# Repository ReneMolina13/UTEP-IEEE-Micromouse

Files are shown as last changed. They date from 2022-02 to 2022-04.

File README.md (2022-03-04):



<!-- PROJECT LOGO -->
</br>
<div align="center">
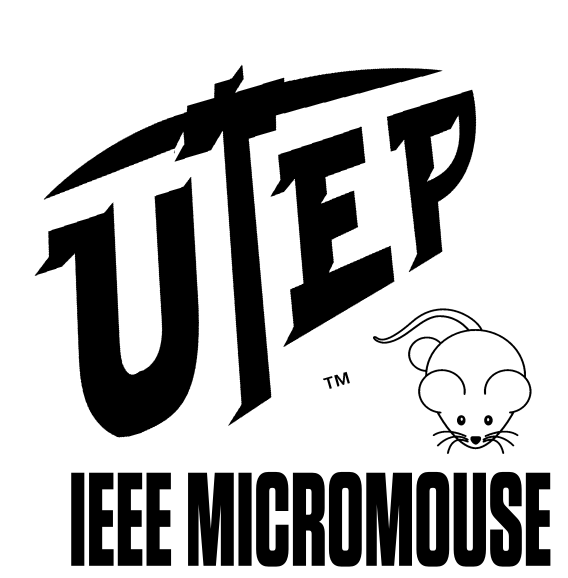
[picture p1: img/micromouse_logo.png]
  
  <h3 align="center">UTEP IEEE Micromouse</h3>
   <p align="center">
     UTEP IEEE Micromouse project repository
     </br>
     <a href="workshops/Intro to micromouse presentation.pdf"><strong>See intro presentation</strong></a>
     </br>
  </p>
</div>

<!-- TABLE OF CONTENTS -->
<details>
  <summary>Table of Contents</summary>
  <ol>
    <li><a href="#about-the-project">About The Project</a></li>
    <li><a href="#contributing">Contributing</a></li>
    <li><a href="#license">License</a></li>
    <li><a href="#contact">Contact</a></li>
    <li><a href="#acknowledgments">Acknowledgments</a></li>
  </ol>
</details>

<!-- ABOUT THE PROJECT -->
## About The Project
</br>
<div align="left">
  IEEE UTEP Micromouse repository where you can find template code, schematics and workshops
  to build and get your mouse working. This repository was designed to be used with the micromouse
  kit shown in the schematics folder. The workshops will guide you through the necessary code to 
  have your mouse solving a micromouse maze.
  
  Take a look at:
  
  - [Schematics](micromouse_arduino_nano_kit/Micromouse_Arduino_Nano.pdf)
  - [Workshops](workshops/)
  - [Code](code_template/)
</div>

<p align="right">(<a href="#top">back to top</a>)</p>

<!-- CONTRIBUTING -->
## Contributing

To contribute, please fork the project and send a pull request or talk to any of the UTEP IEEE officers. For any other questions please use the contact info at the bottom to contact the owner of this repository.
<p align="right">(<a href="#top">back to top</a>)</p>

<!-- LICENSE -->
## License

Distributed under the MIT License. See `LICENSE.txt` for more information.

<p align="right">(<a href="#top">back to top</a>)</p>

<!-- CONTACT -->
## Contact

Alejandro Martinez Acosta - amartinezacosta@miners.utep.edu

Project Link: [https://github.com/amartinezacosta/UTEP-IEEE-Micromouse](https://github.com/amartinezacosta/UTEP-IEEE-Micromouse)

<p align="right">(<a href="#top">back to top</a>)</p>

<!-- ACKNOWLEDGMENTS -->
## Acknowledgments
[University of Texas at El Paso](https://www.utep.edu/)

[IEEE University of Texas at El Paso branch](https://edu.ieee.org/us-utep/)

<p align="right">(<a href="#top">back to top</a>)</p>

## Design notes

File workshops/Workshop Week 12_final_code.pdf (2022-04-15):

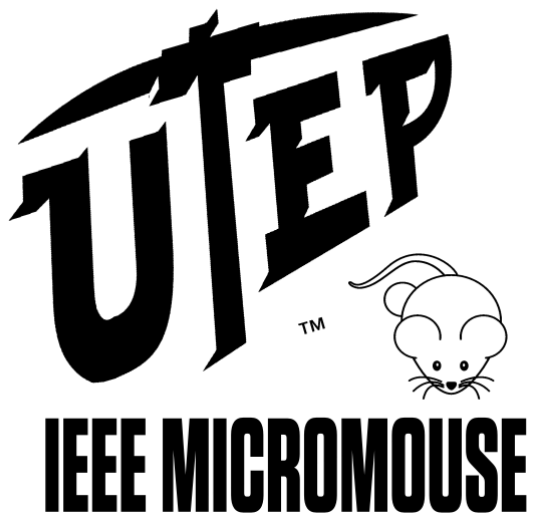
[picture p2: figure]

# Workshop Week 12: Scan walls, bestneighbor, and turn to neighbor

2

## Objective:

## Finish the micromouse code with the final algorithm to reach the center of the maze by

completing the missing code, such as scanning for walls, finding the best neighbor and turning towards the best neighbor.

## Background information:

This week we will look at the final portions of code to solve the maze, thus completing the micromouse project. Last workshop, you were able to find the best path possible to the center of the maze by using the flood fill algorithm. The exercise for the last workshop was to manually

## move the mouse around the maze. Today we will automate the process by writing a set of

functions that will find the best neighbor (open neighbor with lowest cell value), turn towards the best neighbor and scan the maze for new walls.

Before tackling those functions, let us start by thinking about the main and final algorithm to solve the maze. First, we want to run the program until we reach the 0 valued cell. Second, we

## want to always orient and move towards the neighbor that is open and has the lowest cell value. Finally, the mouse must update its position and orientation on the maze as well as

physically on the real maze. In addition, the mouse must add walls to the maze as they are encountered.

## With those requirements in mind, here is the final algorithm to solve the maze:

1. void loop()
2. {
3. /*Get the initial position and heading of the mouse*/
4. int8_t x = mouse_get_x();
5. int8_t y = mouse_get_y();
6. uint8_t heading = mouse_get_heading();
7.
8. /*Run the algorithm until we reached the zero value cell (Center of the maze)*/
9. do
10. {
11. /*Wait for button press or serial console for debugging (Not needed)*/
12. while(digitalRead(BUTTON) != HIGH);
13.
14. /*Scan walls*/
15. scan_walls(x, y, heading);
16.
17. /*Update maze using floodfill*/
18. flood_fill(x, y);
19.
20. /*Get the best neighbor*/
21. uint8_t best_neighbor = find_best_neighbor(x, y); 22.
23. /*Orient mouse towards best neighbor*/
24. turn_best_neighor(best_neighbor);
25.
26. /*Move forward*/
27. move_forward(x, y, best_neighbor);
28.
29. /*Get the position and heading of the mouse*/
30. x = mouse_get_x();

3

31. y = mouse_get_y();
32. heading = mouse_get_heading();
33.
34. /*Print maze, only for debugging (Not needed)*/
35. maze_print();
36. }while(maze_get_value(x, y) != 0);
37.
38. /*Maze solved trap the CPU*/
39. while(1);
40. }
41.

As you can observe, we are placing the final portion of code in the loop function. This is not required, because once we reached the center of the maze, we want to finish our program. You might want to play around and explore on what to do next after we find the center of the maze. One thing that you might consider is to do a second run with the maze already mapped out and with a valid path to center, but this time the mouse does it as fast as possible.

## Scan walls

## To scan the walls, the mouse simply must take a reading on all sensors and check if the

measurements are greater than the wall thresholds.

Now it is easy to think that if the right or left sensor measurements is greater than a threshold, then we simply add a wall to the EAST or WEST. This in fact will give you the wrong result because the orientation of the mouse is not always aligned to the NORTH of the maze and the

## walls are relative to it. Here is a visual example of why this happens:

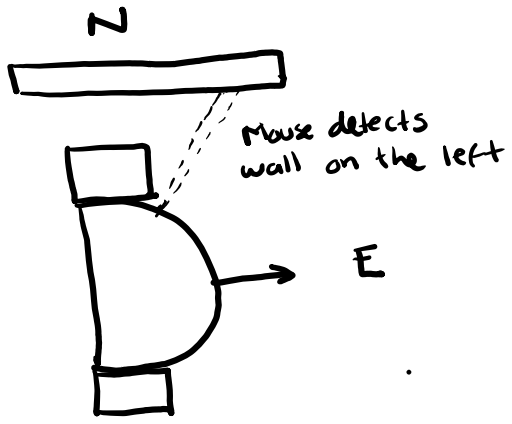
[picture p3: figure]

Figure 1 Adding walls to the maze depends on the orientation of the mouse. The mouse is heading EAST, but we detected a wall on our left. If we simply add the left sensor as an EAST wall, then we will get the wrong wall placement

4

Looking at the image above, you can see that the mouse detected a wall to the left of its sensor. You might be tempted to add the WEST wall of the current cell, but that will be wrong because of the orientation of the mouse. The correct answer is to add a wall to the NORTH. To solve this problem, we are going to shift the orientation of the wall discovered by 1 or 3 depending on the

## heading of the mouse. So, for the image above, we simply shift the current heading of the mouse heading by 3, so we move from EAST to SOUTH to WEST and the finally to NORTH, which

is the correct position of the discovered wall. if we discover a wall to our right, we take the same approach but this time we only shift the wall orientation by one. This is the code to add a

## wall when the left IR sensor measurement is greater than a threshold:

1. /*Threshold for left sensor*/
2. if(ir2 > IR_LEFT_WALL_THRESHOLD)
3. {
4. /*There is a wall on our right*/
5. /*Bit shift heading for correct wall positioning*/
6. uint8_t wall = heading << 3;
7. /*If bigger than 16, then wrap around back to 1*/
8. if(wall > 8)
9. {
10. wall /= 16;
11. }
12.
13. maze_set_wall(x, y, wall);
14. }
15.

Notice that we need to wrap around the wall if it ever gets bigger than 8, this is due to the internal implementation of the maze, and it should be added to your code.

## The final code to scan for walls will look like this:

1. const int IR_FRONT_WALL_THRESHOLD = 700;
2. const int IR_RIGHT_WALL_THRESHOLD = 700;
3. const int IR_LEFT_WALL_THRESHOLD = 700;
4.
5. void scan_walls(int x, int y, uint8_t heading)
6. {
7. /*Measure all IR sensors*/
8. int ir0 = ir_0_read(150);
9. int ir1 = ir_1_read(150);
10. int ir2 = ir_2_read(150);
11. int ir3 = ir_3_read(150);
12.
13. /*Threshold for front sensors*/
14. int ir_front = (ir0 + ir3)/2;
15. if(ir_front > IR_FRONT_WALL_THRESHOLD)
16. {
17. /*There is a wall at the front*/
18. /*Just set the wall to the current heading of the mouse*/
19. maze_set_wall(x, y, heading);
20. }
21.
22. /*Threshold for right sensor*/
23. if(ir1 > IR_RIGHT_WALL_THRESHOLD)
24. {
25. /*There is a wall on our left*/

5

26. /*Bit shift heading for correct wall positioning*/
27. uint8_t wall = heading << 1;
28. /*If bigger than 16, then wrap around back to 1*/
29. if(wall > 8)
30. {
31. wall /= 16;
32. }
33.
34. maze_set_wall(x, y, wall);
35. }
36.
37. /*Threshold for left sensor*/
38. if(ir2 > IR_LEFT_WALL_THRESHOLD)
39. {
40. /*There is a wall on our right*/
41. /*Bit shift heading for correct wall positioning*/
42. uint8_t wall = heading << 3;
43. /*If bigger than 16, then wrap around back to 1*/
44. if(wall > 8)
45. {
46. wall /= 16;
47. }
48.
49. maze_set_wall(x, y, wall);
50. }
51. }
52.

## Find best neighbor

Next up is finding the best neighbor. The best neighbor is always going to be the open cell with the lowest cell value. If you look at the flood fill algorithm, you can observe that there is a section that also tries to find the neighbor with the lowest minimum value. So, we can simply

## repeat that implementation as follows:

1. uint8_t find_best_neighbor(int x, int y)
2. {
3. /*Neighbor offsets for all orientations*/
4. int8_t neighbor_offset[4][2] =
5. {
6. {0, -1},
7. {1, 0},
8. {0, 1},
9. {-1, 0},
10. };
11.
12. /*Get current cell*/
13. cell_t *current = maze_get_cell(x, y);
14. cell_t *neighbor_cell;
15.
16. /*Assume lowest value is the highest distance*/
17. uint8_t lowest_value = 255;
18. /*Assume best neighbor is to the north*/
19. uint8_t best_neighbor = NORTH;
20. for(int i = 0; i < 4; i++)
21. {
22. /*If the neighbor is open...*/
23. if((current->walls & (1 << i)) == 0)

6

24. {
25. /*Get neighbor coordinates*/
26. int8_t nx = x + neighbor_offset[i][0];
27. int8_t ny = y + neighbor_offset[i][1]; 28.
29. /*Get neighbor cell value*/
30. neighbor_cell = maze_get_cell(nx, ny);
31. if(neighbor_cell->value < lowest_value)
32. {
33. /*If this this lower than the previous cell value, then set it as
34. * the new minimum
35. */
36. lowest_value = neighbor_cell->value;
37. best_neighbor = (1 << i);
38. }
39. }
40. }
41.
42. return best_neighbor;
43. }
44.

Observe that we always assume that the best neighbor is to the north. We do this so that if we

## have 2 neighbors of the same value, we always select the one that does not make the mouse

turn.

## Turn towards best neighbor

The next function we need to tackle is turning towards the best neighbor. The input of this function is the desired heading, and the output will obviously be the mouse physically turning

## and the maze updating the heading of the mouse. To do this we must consider the current

heading of the mouse and the desired heading, which will come in the form of NORTH, EAST,

## SOUTH and WEST. Once we know this, we can now physically turn the mouse +90.0, -90.0 or

180.0 degrees.

## To know the angle the mouse has to turn, we must create a truth table as follows:

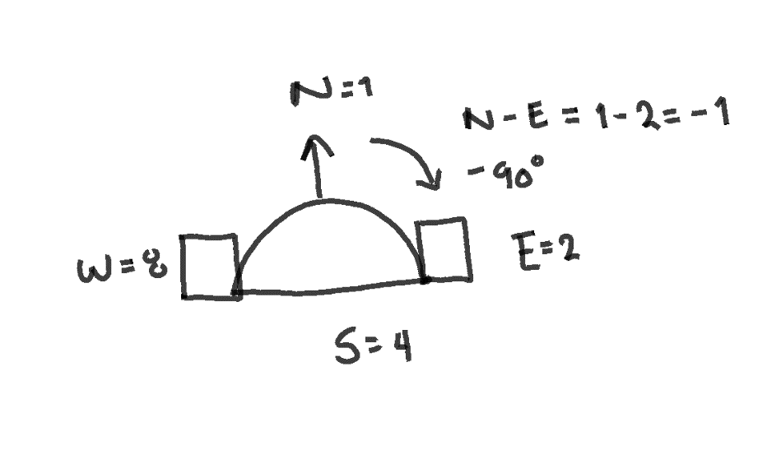
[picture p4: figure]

Figure 2 Basic idea on how we find how the angle and direction of rotation

7

Heading | New Heading | Heading - New Heading | Result
1 | 1 | 0 | 0°
1 | 2 | -1 | -90°
1 | 4 | -3 | 180°
1 | 8 | -7 | 90°
2 | 1 | 1 | 90°
2 | 2 | 0 | 0°
2 | 4 | -2 | -90°
2 | 8 | -6 | 180°
4 | 1 | 3 | 180°
4 | 2 | 2 | 90°
4 | 4 | 0 | 0°
4 | 8 | -4 | -90°
8 | 1 | 7 | -90°
8 | 2 | 6 | 180°
8 | 4 | 4 | 90°
8 | 8 | 0 | 0°
Figure 3 Truth table to turn the mouse based on current and desired heading

Using the table as our guide, we can create a switch statement (https://www.tutorialspoint.com/cprogramming/switch_statement_in_c.htm) to turn the mouse based on the

## result of the heading minus the new heading. The code looks as follows:

1. void turn_best_neighor(uint8_t best_neighbor)
2. {
3. /*Get current heading*/
4. uint8_t heading = mouse_get_heading();
5. /*Relative positioning to best neighbor*/
6. int8_t delta = heading - best_neighbor;
7.
8. /*Truth table to find how much we need to turn*/
9. switch(delta)
10. {
11. case 7: case -1: case -2: case -4:
12. /*Physically turn the mouse*/
13. control_turn(-90.0);
14. break;
15. case -7: case 1: case 2: case 4:
16. /*Physically turn the mouse*/
17. control_turn(90.0);
18. break;
19. case 3: case -3: case 6: case -6:
20. /*Physically turn the mouse*/
21. control_turn(180.0);
22. break;
23. }
24.
25. /*Update heading mouse*/
26. mouse_set_heading(best_neighbor);
27. }
28.

8

Notice that we are using the control_turn function from workshop 9. (https://github.com/amartinezacosta/UTEP-IEEE-Micromouse/blob/main/workshops/Workshop%20Week%209_Turn%20Control.pdf) If you don’t have this function, please go back to and complete this workshop.

## Move forward

## Lastly, we need to move the mouse forward AFTER we orient the mouse towards the best

neighbor. As with the turn_best_neighbor function, we first physically move the mouse, then

## update its position on the maze. The function to do this can be coded as follows:

1. void move_forward(int8_t x, int8_t y, uint8_t heading)
2. {
3. /*Physically move the mouse forward*/
4. control_forward();
5.
6. /*figure out where we need to move the mouse on the map*/
7. switch(heading)
8. {
9. case NORTH:
10. y--;
11. break;
12. case EAST:
13. x++;
14. break;
15. case SOUTH:
16. y++;
17. break;
18. case WEST:
19. x--;
20. break;
21. }
22.
23. /*Set the mouse new position on the map*/
24. mouse_set_x(x);
25. mouse_set_y(y);
26. }
27.

## Look at how we move the mouse based on the heading. Depending on the orientation of the

mouse, if we move forward one cell, then we either increment or decrement the x or y position of the mouse.

Finally, observe that we make use of the control_forward function, which was introduced in workshop 8. (https://github.com/amartinezacosta/UTEP-IEEE-Micromouse/blob/main/workshops/Workshop%20Week%208_Speed%20and%20Wall%20Control.pdf) Again, if you don’t have this function, please read the workshop and complete it.

9

## Exercise:

Complete the micromouse project by writing the scan_walls, find_best_neighbor,

## turn_best_neighbor and move_forward functions into your main sketch. Use the code

template below.

1. #include "micromouse.h"
2. #include "maze.h"
3.
4. uint8_t find_best_neighbor(int x, int y)
5. {
6. }
7.
8. void scan_walls(int x, int y, uint8_t heading)
9. {
10. }
11.
12. void turn_best_neighbor(uint8_t best_neighbor)
13. {
14. }
15.
16. void move_forward(int8_t x, int8_t y, uint8_t heading)
17. {
18. }
19.
20. void setup()
21. {
22. /*Enable serial port for bluetooth*/
23. Serial.begin(9600);
24.
25. /*Initialize maze*/
26. maze_init(MAZE_WIDTH/2, MAZE_HEIGHT/2);
27. mouse_set_x(0);
28. mouse_set_y(MAZE_HEIGHT - 1);
29. }
30.
31. void loop()
32. {
33. /*Get the initial position and heading of the mouse*/
34. int8_t x = mouse_get_x();
35. int8_t y = mouse_get_y();
36. uint8_t heading = mouse_get_heading();
37.
38. /*Run the algorithm until we reached the zero value cell (Center of the maze)*/
39. do
40. {
41. /*Wait for button press or serial console for debugging (Not needed)*/
42. while(digitalRead(BUTTON) != HIGH);
43.
44. /*Scan walls*/
45. //scan_walls(x, y, heading);
46.
47. /*Update maze using floodfill*/
48. flood_fill(x, y);
49.
50. /*Get the best neighbor*/
51. uint8_t best_neighbor = find_best_neighbor(x, y); 52.
53. /*Orient mouse towards best neighbor*/
54. turn_best_neighor(best_neighbor);
55.
56. /*Move forward*/

10

57. move_forward(x, y, best_neighbor);
58.
59. /*Get the position and heading of the mouse*/
60. x = mouse_get_x();
61. y = mouse_get_y();
62. heading = mouse_get_heading();
63.
64. /*Print maze, only for debugging (Not needed)*/
65. maze_print();
66. }while(maze_get_value(x, y) != 0);
67.
68. /*Maze solved trap the CPU*/
69. while(1);
70. }
71.

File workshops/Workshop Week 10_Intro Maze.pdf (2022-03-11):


# Workshop Week 10: Intro to Maze

2

Objective:

Learn how to represent a maze in C, and how to set the walls and values of the maze cells. Learn about data structures and how they can be used to represent a maze cell. Print the maze into a terminal to visualize the maze and mouse position.
Background information:

We are now moving into what we consider the second part of micromouse project, the maze/path planning software. In this second part, we will write the code to represent the maze inside the Arduino’s memory, scan for walls, find the best neighbor and orient the mouse towards the best neighbor. We will also start thinking about the end goal of the micromouse and working towards finishing the final algorithm of the micromouse project.

As of right now, our mouse can move a maze cell distance and turn accurately to a specified angle. This is great if we only want to move on a straight and turn mindlessly, but we know that the mouse should accomplish a specific task, which is reaching the center of the maze. To do this we need to have a path planning algorithm, and to do path planning we need a map of the mouse environment. The map of the micromouse is simple, 8x8 cells each with 4 walls on it’s NORTH, EAST, SOUTH and WEST borders. The cells on the borders can be assumed to always have a wall on its perimeter, so that leave us with mapping the rest of the cells on the maze.

In the interest of time, we will provide you with the code for the maze. You will still be responsible for writing some of the necessary functions to finish the path planning algorithm, but the maze representation and printing functions will be provided to you.

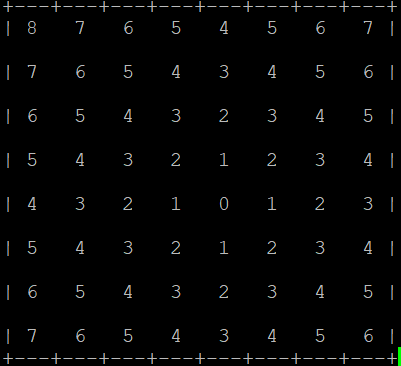
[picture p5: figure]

Figure 1 Printed maze

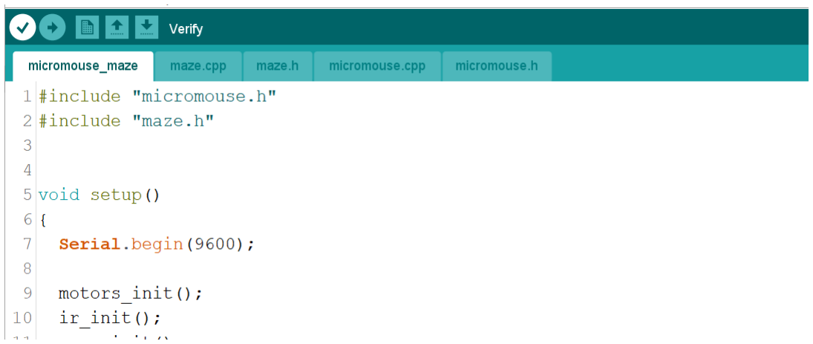
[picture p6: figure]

3

Setup Maze Sketch

To start, download (https://github.com/amartinezacosta/UTEP-IEEE-Micromouse/tree/main/src) and copy the maze.cpp and maze.h files into your sketch folder. You might have to close and open the Arduino sketch to see the files. You should see a project structure with the files shown below.

Verify and upload the sketch to your Arduino.

Initializing the Maze and Mouse position

Now that you have the maze files into your sketch, we can start using them to initialize the maze, the mouse position within the maze and visualize the maze and mouse position on a serial console.

Write the following code into your Arduino Sketch:

1. #include "micromouse.h"
2. #include "maze.h"
3.
4. void setup()
5. {
6. Serial.begin(9600);
7.
8. motors_init();
9. ir_init();
10. gyro_init();
11.
12. /*Intialize maze with goal position at the center*/
13. maze_init(MAZE_WIDTH/2, MAZE_HEIGHT/2);
14.
15. /*Initailize mouse position at the bottom
16. left corner of the maze. Initialize heading to NORTH*/
17. mouse_set_heading(NORTH);

4

18. mouse_set_x(0);
19. mouse_set_y(MAZE_HEIGHT-1);
20.
21. /*Print maze. This is where you could use the
22. * HC-05 to send the maze wirelessly to your laptop*/
23. maze_print();
24. }
25.
26. void loop()
27. {
28. }
29.

Upload the code into your Arduino. To visualize the maze download Putty, (https://www.putty.org/) open it and the select the following options

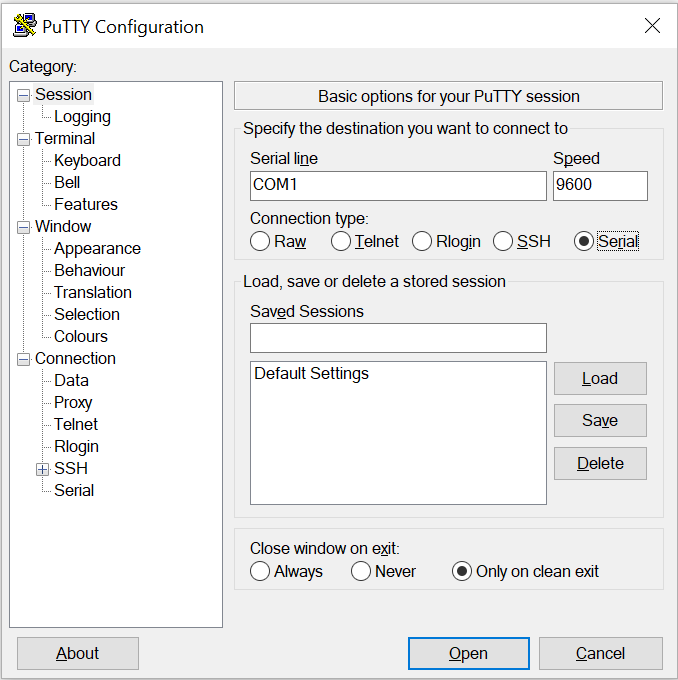
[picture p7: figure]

Figure 2 Putty setting for maze print output

Change the COM1 to your Arduino’s COM port number. Once you open the serial terminal, you should see the maze with the mouse at the bottom left corner.

5

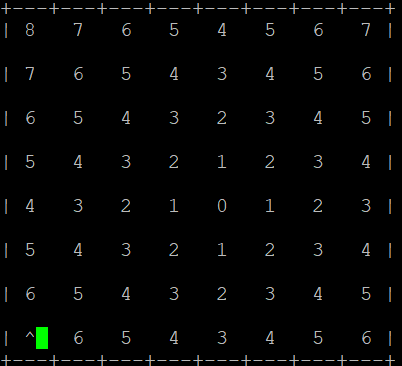
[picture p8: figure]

Figure 3 Maze and Mouse visualization. The mouse is represented by a caret symbol

Setting Walls on the Maze

You can set walls on the maze by using the function

1. int8_t maze_set_wall(uint8_t x, uint8_t y, uint8_t wall);

Where x and y are the row and column number of the maze and wall specifies which wall is to be set. For example, to set row 7 column 0 EAST wall, we can call the function with the following parameters

1. maze_set_wall(0, 7, EAST);

Write the following program to initialize and set the EAST wall form the initial position of the mouse

1. #include "micromouse.h"
2. #include "maze.h"
3.
4. void setup()
5. {
6. Serial.begin(9600);
7.
8. motors_init();
9. ir_init();
10. gyro_init();
11.
12. /*Intialize maze with goal position at the center*/
13. maze_init(MAZE_WIDTH/2, MAZE_HEIGHT/2);
14.
15. /*Initailize mouse position at the bottom
16. left corner of the maze. Initialize heading to NORTH*/
17. mouse_set_heading(NORTH);
18. mouse_set_x(0);

6

19. mouse_set_y(MAZE_HEIGHT-1); 20.
21. /*Set a wall*/
22. maze_set_wall(0, 7, EAST);
23.
24. /*Print maze. This is where you could use the
25. * HC-05 to send the maze wireleslly to your laptop*/
26. maze_print();
27. }
28.
29. void loop()
30. {
31. }
32.

The output of the maze should look as follows:

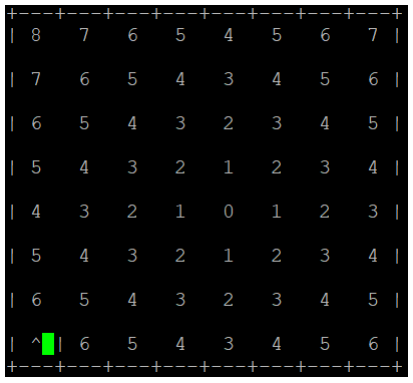
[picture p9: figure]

Figure 4 Maze with EAST wall at 0,7

Setting Mouse position and heading

We can also set the mouse position and heading by using the following functions,

1. void mouse_set_heading(uint8_t heading);
2. void mouse_set_x(int8_t x);
3. void mouse_set_y(int8_t y);

As an example, for the micromouse competition the mouse starts at one of the corners of the maze, so we can set the mouse initial position in x = 0 and y = 7 facing NORTH. Write the following code to move the mouse to a different position

7

1. #include "micromouse.h"
2. #include "maze.h"
3.
4. void setup()
5. {
6. Serial.begin(9600);
7.
8. motors_init();
9. ir_init();
10. gyro_init();
11.
12. /*Intialize maze with goal position at the center*/
13. maze_init(MAZE_WIDTH/2, MAZE_HEIGHT/2);
14.
15. /*Initailize mouse position. Initialize heading to WEST*/
16. mouse_set_heading(WEST);
17. mouse_set_x(4);
18. mouse_set_y(5);
19.
20. /*Set a wall*/
21. maze_set_wall(0, 7, EAST);
22.
23. /*Print maze. This is where you could use the
24. * HC-05 to send the maze wireleslly to your laptop*/
25. maze_print();
26. }
27.
28. void loop()
29. {
30. }
31.

The output of the maze should be as follows

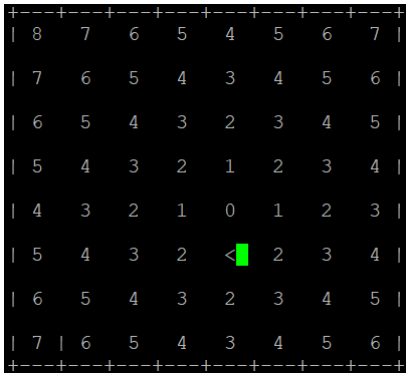
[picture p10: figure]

Figure 5 Changing mouse position and heading

8

Exercise:

Have the mouse move accept input form your computer keyboard so that it can move and head NORTH, EAST, SOUTH or WEST. You can accomplish this by using the Serial.read() and Serial.available() functions. Print the maze output into putty to visualize the position and heading of the mouse.

1. #include "micromouse.h"
2. #include "maze.h"
3.
4. void setup()
5. {
6. Serial.begin(9600);
7.
8. motors_init();
9. ir_init();
10. gyro_init();
11.
12. /*Intialize maze with goal position at the center*/
13. maze_init(MAZE_WIDTH/2, MAZE_HEIGHT/2);
14.
15. /*Initailize mouse position at the bottom
16. left corner of the maze. Initialize heading to NORTH*/
17. mouse_set_heading(WEST);
18. mouse_set_x(4);
19. mouse_set_y(5);
20.
21. /*Set a wall*/
22. maze_set_wall(0, 7, EAST);
23.
24. /*Print maze. This is where you could use the
25. * HC-05 to send the maze wireleslly to your laptop*/
26. maze_print();
27. }
28.
29. void loop()
30. {
31. while(!Serial.available());
32. int c = Serial.read();
33. /*if c == ‘w’ move NORTH*/
34. /*if c == ‘d’ move EAST*/
35. /*if c == ‘s’ move SOUTH*/
36. /*if c == ‘a’ move WEST*/
37. maze_print();
38. }
39.

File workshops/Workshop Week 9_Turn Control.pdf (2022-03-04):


# Workshop Week 9: Turn control

2

Objective:

Control turn angles of the mouse in clockwise and counterclockwise rotations. Use the concepts from previous workshops to design a turn proportional controller. Finally, write and test the software for this week’s workshop
Background information:

From previous workshops, we learned how to use proportional controllers to reach target distances from a maze cell and maze walls. This week we will design a turn controller for the mouse. The goal of this controller is to turn at accurate angles, so that we can precisely stop and turn when we find a wall in front of the mouse.

The same ideas form the previous controllers will be applied on this turn controller. First, we need to compute the error from a set angle and the actual angle. This is simply represented as:

Angleerror = Angletarget − Angleactual

This error can be amplified and used as the output for the motors. The only difference this time is that both wheels must go in opposite directions, so the output of one motor will always be the negative of the other. The equations to achieve the motor outputs are as follows:

turnoutput = kpturn ∗ Angleerror

Outputleft = turnoutput

Outputrigℎt = −turnoutput

Our controller will correct for any disturbance, overshooting or undershooting our target angle. The turn profile we will use for this micromouse is the one shown in figure 1. Notice how the wheels run in opposite directions to create a tight turn.

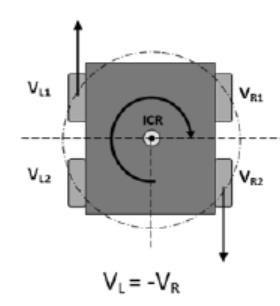
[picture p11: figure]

Figure 1 Turn profile for micromouse

3

Get gyro yaw angle

We are going to use the code from week 6 workshop to measure the yaw angle of the mouse. If you recall, using a gyroscope will allow us to measure the turn angle of the mouse by numerical integrating the raw output of the sensor. If you have not read this workshop, please do as most of the code will not be explained in here.

Let us enclose the gyroscope initialization and measurement into a couple of functions.

1. void gyro_init(void)
2. {
3. gyro.initialize();
4. gyro.CalibrateGyro();
5. }
6.
7. float get_angle(float dt)
8. {
9. int16_t raw_yaw_rate = gyro.getRotationZ();
10. float yaw_rate = (float)raw_yaw_rate / 131.0;
11. float yaw_angle = yaw_rate * dt;
12.
13. return yaw_angle;
14. }
15.

Add these functions to your micromouse.cpp and micromouse files.

Main turn control loop

The control loop for the turn controller is vastly like the previous controller loops we designed. Again, the only differences on this controller are the sensor source and the motor output calculations. The code for this controller is as follows:

1. const float MIN_TURN_ERROR = 1.0;
2. const float turn_kp = 30.0;
3.
4. void control_turn(float target_angle)
5. {
6. /*Keep running the control loop until the error is less that the
7. * minimum specified error (MIN_TURN_ERROR)
8. */
9. float yaw_angle = 0.0;
10. float dt = 0.0;
11. float t0;
12. float turn_error;
13. do
14. {
15. t0 = millis() / 1000.0;
16.
17. /*Read gyro yaw angle, remember that this is a measurement for
18. * this time period so we need to sum the previous angle measurements
19. */
20. yaw_angle += get_angle(dt);
21.

4

22. /*Compute turn error*/
23. turn_error = target_angle - yaw_angle;
24.
25. /*Proportional error for turn. Clamp output value*/
26. float turn_output = clamp(turn_kp*turn_error, 80.0, -80.0); 27.
28. /*Calculate final output speed for each wheel*/
29. int left_output = (int)(-turn_output);
30. int right_output = (int)(turn_output);
31.
32. /*Find the turn direction of each wheel. Check the find_direction function*/
33. bool left_dir = find_direction(left_output);
34. bool right_dir = find_direction(right_output);
35.
36. /*Set speed and direction to motors*/
37. motor_0_speed(abs(right_output), right_dir);
38. motor_1_speed(abs(left_output), left_dir);
39.
40. /*delay the control loop and calculate delta time*/
41. delay(50);
42. dt = millis()/1000.0 - t0;
43. }while(fabs(turn_error) > MIN_TURN_ERROR);
44.
45. /*Stop both motors*/
46. motor_0_speed(0, true);
47. motor_1_speed(0, true);
48. }
49.

A few things to notice:

1. Turn speed affects the performance of the controller by overshooting or undershooting the set angle
2. The delay time also plays an important role on the controller. Making the delay shorter will increase the gyroscope drift
3. As in last week workshop, the proportional coefficient amplifies the velocity response to the error of the turn angle
4. The micromouse will always overshoot the target position. We don’t know exactly why that is, but our best guess is that the gyroscope is not positioned exactly at the center of the mouse.

See that we also use the clamp() and find_direction() functions from workshop 8. If you do not have those, please go and see workshop 8. Add this control function to your micromouse.cpp and micromouse.h files.

5

Using the turn control on your sketch

Now you can use the code on your main sketch to turn the mouse to a given angle. Try this on your main sketch

1. #include "micromouse.h" 2.
3. void setup()
4. {
5. /*Initialize motors*/
6. motors_init();
7. gyro_init();
8. ir_init();
9. /*Initialize serial console*/
10. Serial.begin(9600);
11. }
12.
13. void loop()
14. {
15. /*Wait for button press*/
16. while(digitalRead(BUTTON) != HIGH);
17. delay(1500);
18.
19. control_turn(75.0);
20.
21. /*Wait for button press*/
22. while(digitalRead(BUTTON) != HIGH);
23. delay(1500);
24.
25. control_turn(-75.0);
26. }
27.

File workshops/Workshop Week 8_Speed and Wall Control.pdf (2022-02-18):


# Workshop Week 8: Micromouse wheel positionmismatch and wall control

2

## Objective:

Enhance the forward control with wall distance and wheel position mismatch compensation. Measure distance from wall and calculate error. Measure encoder wheel and calculate position mismatch. Write the control software to compensate for these errors. Understand the control system design for the mouse.

## Background information:

## Last week we worked on distance control using the encoder measurements and a proportional

controller. This week we will enhance the controller by adding a wheel position mismatch and a wall distance controller.

## As explained last week, we can compensate for errors between a desired distance and the

actual distance. Our controller will proportionally fix the error distance so that we match it to

## our desired distance. Using this idea, we can use desired targets and actual sensor

measurements to compensate for other disturbances or errors in our mouse.

On the first workshops, some of you noticed that the mouse was steering towards one side even though the speed and direction on both wheels was the same. This is caused by the weight distribution of the mouse and the manufacturing variances between both motors. We want to prevent this behavior from occurring, so we are going to add another proportional controller that will try to minimize the position mismatch between wheels. To design this

control, let’s first think about the best-case scenario for our mouse motors. If both wheels are

## always moving at the same speed, then both encoders should read the same value. Now, we know this is not happening because we can see the mouse steering one way or the other, so any deviation from this desired measurement is our error. This can be translated as

wℎeelerror = 0 − (rigℎtencoder − leftencoder)

wℎeelerror = leftencoder − rigℎtencoder

Notice that our desired value in this case is zero since we do not any difference between our wheels.

Another scenario that we are trying to prevent is collision against walls. To do this, we must drive the mouse perfectly at the center of the maze walls. This is of course impossible in practice, and at some point, the mouse will crash against a wall. if you been paying attention,

## then you know that we can correct for this by adding a proportional controller that

compensates for the error on a desired wall distance. In this case the sensor that will measure this difference is the right and left infrared sensors. So, as we did with the wheel position

## mismatch controller, let’s define some equations for our error:

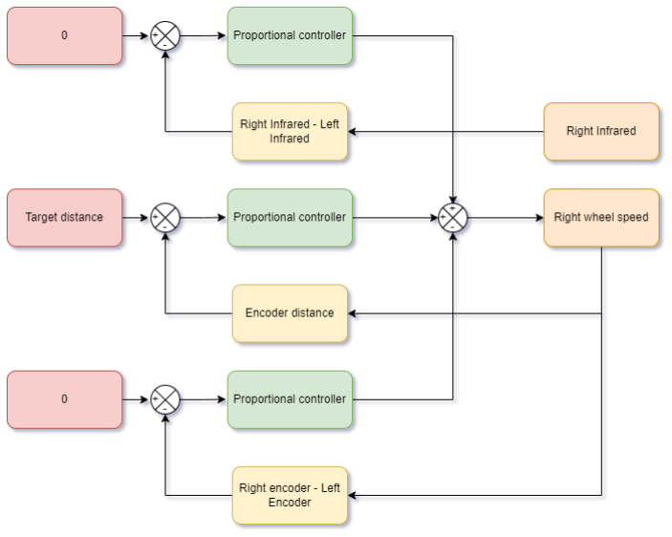
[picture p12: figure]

3

Wallerror−left = infraredleft−desired − infraredleft−actual

Wallerror−rigℎt = infraredrigℎt−desired − infraredrigℎt−actual

Wallerror−center = wallerror−rigℎt − wallerror−left

If infraredleft−desired and infraredrigℎt−desired are equal, then the Wallerror−center can be

## reduced to

Wallerror−center = infraredleft−actual − infraredrigℎt−actual

## We want to minimize this off-center error, so again our target should be to always have a measurement of 0 between the left and right infrared sensors (assuming they both measure

the same value).

Look at figure 1 and 2 to graphically see how these controllers interact with each other. If you still have aa difficult time understanding the diagrams or any of the concepts, please reach out to any IEEE officer for help.

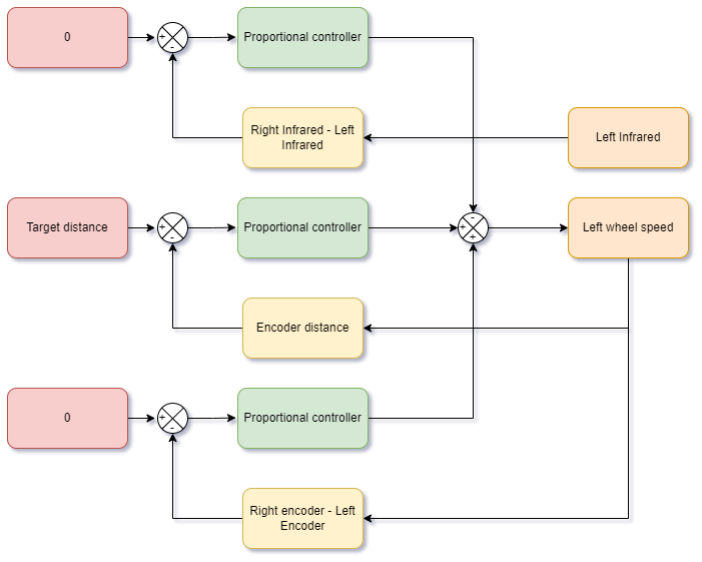
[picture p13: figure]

Figure 2 Left wheel controller diagram | Figure 1 Right wheel controller diagram

4

## Clamp and find_direction functions

## Before diving into the control software, we need to organize the code from last week into

smaller chunks. Clamping values and finding the direction of wheels can be abstracted into

## functions as following:

1. float clamp(float value, float max, float min)
2. {
3. if(value > max)
4. {
5. value = max;
6. }
7. else if(value < min)
8. {
9. value = min;
10. }
11.
12. return value;
13. }
14.
15. bool find_direction(int value)
16. {
17. bool dir;
18. if(value > 0)
19. {
20. dir = true;
21. }
22. else if(value < 0)
23. {
24. dir = false;
25. }
26.
27. return dir;
28. }

## We can now clamp the value for the controllers as follows:

1. float distance_output = clamp(distance_kp*distance_error, 150.0, -150.0);

And find the direction of a wheel based on its output,

1. bool left_dir = find_direction(left_output);

5

## Calculating the errors and outputs

Next, we need to calculate the errors from our different controllers. Following the equations from the background information section and figures 1 and 2 we can write the following code:

1. const long int MIN_ERROR = 50;
2. const long int target_distance = 1090;
3.
4. void control_forward(void)
5. {
6. /*Keep running the control loop until the error is less that the
7. * minimum specified error (MIN_ERROR)
8. */
9. int distance_error;
10. do
11. {
12. /*Read encoder for left and right motors. Estimate
13. * mouse traveled distance by taking the average of
14. * both encoders.
15. */
16. long int r_count = right_encoder.read();
17. long int l_count = -left_encoder.read();
18. long int encoder_distance = (r_count + l_count) / 2;
19. int r_ir = ir_1_read(150);
20. Int l_ir = ir_2_read(150);
21.
22. /*Compute distance, speed mismatch and distance from wall error*/
23. distance_error = target_distance - encoder_distance;
24. int mismatch_error = r_count - l_count;
25. int ir_error = r_ir - l_ir;
26.
27. delay(20);
28. }while(abs(distance_error) > MIN_ERROR); 29.
30. /*Stop both motors*/
31. motor_0_speed(0, true);
32. motor_1_speed(0, true); 33.
34. /*Reset encoders*/
35. right_encoder.write(0);
36. left_encoder.write(0);
37. }
38.

Notice that we now have 3 sources of errors that we want to correct,

## 1. Distance error 2. Wheel position mismatch error 3. Infrared distance from wall error

To minimize this error, we will use the proportional error code from last week. This time we need 3 proportional parameters distancekp, mismatcℎkp,IRkp to tune the controller output.

Also, we do not want one our controllers to saturate the output, as this will leave the other controllers without any control output to correct its error. Using the clamp function can we

6

limit the output of the controllers to a percentage of the maximum speed (+-255). In this case

## we assigned the following values of the maximum speed:

## distanceoutput = ±150

## mismatcℎoutput = ±50

IRoutput = ±50

Which corresponds to the 58%, 19% and 19% of the max speed value.

The code for the output with clamping can be written as follows,

1. const long int MIN_ERROR = 50;
2. const long int target_distance = 1090;
3. const float distance_kp = 1.0;
4. const float speed_kp = 2.0;
5. const float ir_kp = 2.0;
6.
7. void control_forward(void)
8. {
9. /*Keep running the control loop until the error is less that the
10. * minimum specified error (MIN_ERROR)
11. */
12. int distance_error;
13. do
14. {
15. /*Read encoder for left and right motors. Estimate
16. * mouse traveled distance by taking the average of
17. * both encoders.
18. */
19. long int r_count = right_encoder.read();
20. long int l_count = -left_encoder.read();
21. long int encoder_distance = (r_count + l_count) / 2;
22. int r_ir = ir_1_read(150);
23. int l_ir = ir_2_read(150);
24.
25. /*Compute distance, speed mismatch and distance from wall error*/
26. distance_error = target_distance - encoder_distance;
27. int mismatch_error = r_count - l_count;
28. int ir_error = r_ir - l_ir;
29.
30. /*Proportional error for all of our errors. Clamp values for all outputs
31. Check the function clamp*/
32. float distance_output = clamp(distance_kp*distance_error, 150.0, -150.0);
33. float mismatch_output = clamp(speed_kp*mismatch_error, 50.0, -50.0);
34. float ir_output = clamp(ir_kp*ir_error, 50.0, -50.0);
35.
36. delay(20);
37. }while(abs(distance_error) > MIN_ERROR);
38.
39. /*Stop both motors*/
40. motor_0_speed(0, true);
41. motor_1_speed(0, true); 42.
43. /*Reset encoders*/
44. right_encoder.write(0);
45. left_encoder.write(0);
46. }
47.

7

## Wall missing from one side

Our controllers will work fine if we have both walls at each side of the mouse. Unfortunately, the maze has sections that have only one wall. This will cause the mouse to steer towards the empty space. To solve this, we need to detect whenever there is not a wall on one of the sides of the mouse, and artificially set the measurement as if there was a wall there.

Add this code to the previous section,

1. const int RIGHT_IR_THRESHOLD = 200;
2. const int LEFT_IR_THRESHOLD = 200;
3. const long int MIN_ERROR = 50;
4. const long int target_distance = 1090;
5. const float distance_kp = 1.0;
6. const float speed_kp = 2.0;
7. const float ir_kp = 2.0;
8.
9. void control_forward(void)
10. {
11. /*Keep running the control loop until the error is less that the
12. * minimum specified error (MIN_ERROR)
13. */
14. int distance_error;
15. do
16. {
17. /*Read encoder for left and right motors. Estimate
18. * mouse traveled distance by taking the average of
19. * both encoders.
20. */
21. long int r_count = right_encoder.read();
22. long int l_count = -left_encoder.read();
23. long int encoder_distance = (r_count + l_count) / 2;
24.
25. /*Read infrared sensors. Ideally both infrared sensors
26. * should read the same value form the wall, so for our error
27. * we can do r_infrared - l_infrared. Check if there is no wall
28. * one side or the other since this will cause the mouse go towards one wall
29. */
30. int r_ir = ir_1_read(150);
31. int l_ir = ir_2_read(150);
32.
33. if(r_ir < RIGHT_IR_THRESHOLD)
34. {
35. /*force "good measurement*/
36. r_ir = 700;
37. }
38. if(l_ir < LEFT_IR_THRESHOLD)
39. {
40. /*force "good measurement*/
41. l_ir = 700;
42. }
43.
44. /*Compute distance, speed mismatch and distance from wall error*/
45. distance_error = target_distance - encoder_distance;
46. int mismatch_error = r_count - l_count;
47. int ir_error = r_ir - l_ir;
48.
49. /*Proportional error for all of our errors. Clamp values for all outputs

8

50. Check the function clamp*/
51. float distance_output = clamp(distance_kp*distance_error, 150.0, -150.0);
52. float mismatch_output = clamp(speed_kp*mismatch_error, 50.0, -50.0);
53. float ir_output = clamp(ir_kp*ir_error, 50.0, -50.0);
54.
55. delay(20);
56. }while(abs(distance_error) > MIN_ERROR);
57.
58. /*Stop both motors*/
59. motor_0_speed(0, true);
60. motor_1_speed(0, true); 61.
62. /*Reset encoders*/
63. right_encoder.write(0);
64. left_encoder.write(0);
65. }
66.

## Output functions for wheels

Finally, we can calculate the output speed and direction of the wheels. Remember that we need to mix the output of the proportional controllers into a single output. The following equation shows how to combine the outputs for the left and right wheel speed.

leftoutput = distanceoutput + mismatcℎoutput − IRoutput

rigℎtoutput = distanceoutput − mismatcℎoutput + IRoutput

For the direction, we can use the find_direction function we wrote earlier,

1. bool left_dir = find_direction(left_output);
2. bool right_dir = find_direction(right_output);

## Combining the code from the previous sections will yield this final code

1. const int RIGHT_IR_THRESHOLD = 200;
2. const int LEFT_IR_THRESHOLD = 200;
3. const long int MIN_ERROR = 50;
4. const long int target_distance = 1090;
5. const float distance_kp = 1.0;
6. const float speed_kp = 2.0;
7. const float ir_kp = 2.0;
8.
9. void control_forward(void)
10. {
11. /*Keep running the control loop until the error is less that the
12. * minimum specified error (MIN_ERROR)
13. */
14. int distance_error;
15. do
16. {
17. /*Read encoder for left and right motors. Estimate
18. * mouse traveled distance by taking the average of
19. * both encoders.

9

20. */
21. long int r_count = right_encoder.read();
22. long int l_count = -left_encoder.read();
23. long int encoder_distance = (r_count + l_count) / 2;
24.
25. /*Read infrared sensors. Ideally both infrared sensors
26. * should read the same value form the wall, so for our error
27. * we can do r_infrared - l_infrared. Check if there is no wall
28. * one side or the other since this will cause the mouse go towards one wall
29. */
30. int r_ir = ir_1_read(150);
31. int l_ir = ir_2_read(150);
32.
33. if(r_ir < RIGHT_IR_THRESHOLD)
34. {
35. /*force "good measurement*/
36. r_ir = 700;
37. }
38. if(l_ir < LEFT_IR_THRESHOLD)
39. {
40. /*force "good measurement*/
41. l_ir = 700;
42. }
43.
44. /*Compute distance, speed mismatch and distance from wall error*/
45. distance_error = target_distance - encoder_distance;
46. int mismatch_error = r_count - l_count;
47. int ir_error = r_ir - l_ir;
48.
49. /*Proportional error for all of our errors. Clamp values for all outputs
50. Check the function clamp*/
51. float distance_output = clamp(distance_kp*distance_error, 150.0, -150.0);
52. float mismatch_output = clamp(speed_kp*mismatch_error, 50.0, -50.0);
53. float ir_output = clamp(ir_kp*ir_error, 50.0, -50.0);
54.
55. /*Calculate final output speed for each wheel*/
56. int left_output = ((int)distance_output + (int)(mismatch_output) - (int)(ir_output));
57. int right_output = ((int)distance_output - (int)(mismatch_output) + (int)(ir_output)); 58.
59. /*Find the turn direction of each wheel. Check the find_direction function*/
60. bool left_dir = find_direction(left_output);
61. bool right_dir = find_direction(right_output);
62.
63. motor_0_speed(abs(right_output), right_dir);
64. motor_1_speed(abs(left_output), left_dir); 65.
66. delay(20);
67. }while(abs(distance_error) > MIN_ERROR); 68.
69. /*Stop both motors*/
70. motor_0_speed(0, true);
71. motor_1_speed(0, true); 72.
73. /*Reset encoders*/
74. right_encoder.write(0);
75. left_encoder.write(0);
76. }
77.

10

## Exercise:

## Place the previous code into your micromouse.cpp and micromouse.h code. Call your code on

the sketch file as follows.

1. #include "micromouse.h" 2.
3. void setup()
4. {
5. /*Initialize motors*/
6. motors_init();
7. ir_init();
8. /*Initialize serial console*/
9. Serial.begin(9600);
10. }
11.
12. void loop()
13. {
14. /*Wait for button press*/
15. while(digitalRead(BUTTON) != HIGH);
16. delay(1500);
17.
18. control_forward();
19. }
20.

## Use the maze to see that the mouse is staying in between the walls of the mouse, is not

steering and it moves the desired distance each time.

## If you prefer, write all of the code into the sketch file and test it this way

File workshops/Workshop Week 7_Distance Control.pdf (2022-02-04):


# Workshop Week 7: Micromouse distance control

2

## Objective:

Traverse one cell distance accurately. Use classical control theory to achieve distance control. Learn the basics of control theory and proportional control loops. Implement a proportional controller in software.

## Background information:

## Now that we have a firm grasp on basic hardware control, we are ready to proceed into the

next section of the workshops. This section depends on everything we have learned and done so far. For this week, we will have a brief introduction on system control theory and how to

## apply it to minimize the distance error between a target distance and the actual mouse

distance.

System control theory deals with the analysis and design of control models and algorithms to

## drive dynamical systems to a desired state. System control theory has applications on

automation, robotics, electronics, finance and numerous other fields in engineering, science

## and economics. In our case, we can apply control theory to correct for any errors on the traveled distance, turning angle, speed mismatch between wheels and mouse distance from

walls.

Before diving into code and theory, let us explain why we even need to use control systems in

## our mouse. As of right now, the mouse only uses thresholds to stop whenever it reaches a

certain distance. This poses a problem because our mouse builds momentum as it accelerates.

## Starting and stopping the mouse in this way will cause it to overshoot and undershoot the

desired travel distance. So, for example, on 10 different tries, we could measure the mouse going over the distance line 7 times and under it 3 times. Introducing a control system will help us minimize this error if we take the time to tune it properly.

Furthermore, we can design other control systems to compensate for error on wheel speeds, turning angle and distance from walls using infrared sensors. With that in mind, let’s introduce

## a figure that shows a practical control loop scheme:

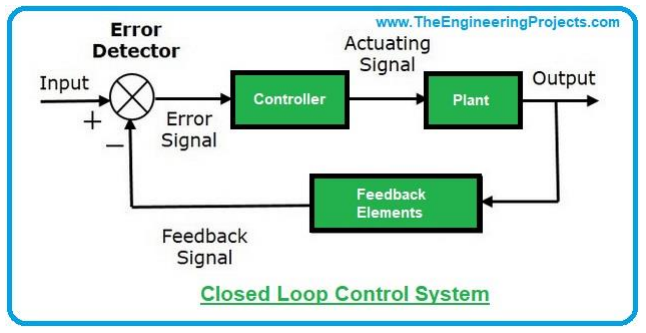
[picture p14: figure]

Figure 1 closed loop control system diagram

3

## The figure shows the general diagram for a control system, and while this is useful to

understand a generic control scheme, it is not obvious how in translates to our micromouse, so let’s begin by explaining it.

## INPUT → Motor Speed ERROR SIGNAL → Target encoder distance – Actual encoder distance CONTROLLER → Proportional gain * ERROR SIGNAL PLANT → DC motor FEEDBACK ELEMENTS → Actual encoder distance OUTPUT → Motor speed

Hopefully you can see that this controller scheme constantly uses encoder measurements to try and achieve the desired encoder set target. The error is calculated by subtracting the actual encoder distance to the desired encoder distance. Then we use the error to modify the speed of the motors. So, if we have a big error the motors will go faster, and as the error goes to zero the speed also goes to zero. We can control how aggressive our controller corrects for the error by using a proportional coefficient. This control scheme is known as a proportional controller, and it is widely used in robotics.

## Distance control with proportional gain

At this point you might be confused about how to implement such a control system in software, especially since there are no clear mathematical equations that can be translated into code. So, for completeness, let’s introduce some equations that can be derived from looking at figure 1:

## error = target − actual

## control = kp ∗ error

Where,

## target = desired distance in encoder counts

## actual = current distance in encoder counts

## kp = proportional coefficient

The control variable will be used as the output speed to our motors and the actual encoder

## measurement is the average between the left and right encoders. We can now convert these set of equations into code:

4

1. #include <Encoder.h>
2. #include "micromouse.h"
3.
4. Encoder right_encoder(ENCODER_0_CHA, ENCODER_0_CHB);
5. Encoder left_encoder(ENCODER_1_CHA, ENCODER_1_CHB);
6.
7. /*One cell distance is approximately 1090 encoder counts*/
8. long int target_distance = 1090;
9. /*Proportional gain coefficient*/
10. float kp = 0.001;
11.
12. void setup()
13. {
14. /*Initialize motors*/
15. motors_init();
16. /*Initialize serial console*/
17. Serial.begin(9600);
18. }
19.
20. void loop()
21. {
22. /*Read encoder for left and right motors. Estimate
23. * mouse traveled distance by taking the average of
24. * both encoders.
25. */
26. long int r_count = right_encoder.read();
27. long int l_count = -left_encoder.read();
28. long int encoder_distance = (r_count + l_count) / 2; 29.
30. /*Distance control loop*/
31. /*Compute error*/
32. long int error = target_distance - encoder_distance;
33. /*Proportional action*/
34. float output = kp*error;
35.
36. /*Move motors at specified velocity*/
37. motor_0_speed((int)output, true);
38. motor_1_speed((int)output, true);
39. }

The code above will correct the error, but there are still a few issues we need to solve in order

## to make this control algorithm practical. The 3 main issues are:

## 1. Determine motor direction based on the sign of the output 2. Clamp output values to a specific MAX_SPEED and MIN_SPEED 3. Make control system repeatable. Once we achieved the desired distance stop

the motors and reset encoders so that we can run the control loop again.

5

## Motor Direction

## To determine the direction of the motors we can write this code on lines 41-49

1. #include <Encoder.h>
2. #include "micromouse.h"
3.
4. Encoder right_encoder(ENCODER_0_CHA, ENCODER_0_CHB);
5. Encoder left_encoder(ENCODER_1_CHA, ENCODER_1_CHB);
6.
7. /*One cell distance is approximately 1090 encoder counts*/
8. long int target_distance = 1090;
9. /*Proportional gain coefficient*/
10. float kp = 0.001;
11.
12. void setup()
13. {
14. /*Initialize motors*/
15. motors_init();
16. /*Initialize serial console*/
17. Serial.begin(9600);
18. }
19.
20. void loop()
21. {
22. /*Read encoder for left and right motors. Estimate
23. * mouse traveled distance by taking the average of
24. * both encoders.
25. */
26. long int r_count = right_encoder.read();
27. long int l_count = -left_encoder.read();
28. long int encoder_distance = (r_count + l_count) / 2; 29.
30. /*Distance control loop*/
31. /*Compute error*/
32. error = target_distance - encoder_distance;
33. /*Proportional action*/
34. float output = kp*error;
35.
36. /*Find the direction of rotation for the wheels*/
37. bool direction;
38. if(output > 0)
39. {
40. direction = true;
41. }
42. else if(output < 0)
43. {
44. direction = false;
45. }
46.
47. /*Move motors at specified velocity*/
48. motor_0_speed((int)output, direction);
49. motor_1_speed((int)output, direction);
50. }
51.

6

## Control output clamping

Next, we need to clamp the values to a specific MAX and MIN speed. If we don’t include this our control loop won’t be able to limit the speed in case the error is too big or too small and our proportional coefficient is not well tuned. This can easily overwhelm a system and cause violent reactions to small error variations.

1. #include <Encoder.h>
2. #include "micromouse.h"
3.
4. Encoder right_encoder(ENCODER_0_CHA, ENCODER_0_CHB);
5. Encoder left_encoder(ENCODER_1_CHA, ENCODER_1_CHB); 6.
7. const long int MAX_SPEED = 200;
8. const long int MIN_SPEED = 70;
9.
10. /*One cell distance is approximately 1090 encoder counts*/
11. long int target_distance = 1090;
12. /*Proportional gain coefficient*/
13. float kp = 0.001;
14.
15. void setup()
16. {
17. /*Initialize motors*/
18. motors_init();
19. /*Initialize serial console*/
20. Serial.begin(9600);
21. }
22.
23. void loop()
24. {
25. /*Read encoder for left and right motors. Estimate
26. * mouse traveled distance by taking the average of
27. * both encoders.
28. */
29. long int r_count = right_encoder.read();
30. long int l_count = -left_encoder.read();
31. long int encoder_distance = (r_count + l_count) / 2; 32.
33. /*Distance control loop*/
34. /*Compute error*/
35. error = target_distance - encoder_distance;
36. /*Proportional action*/
37. float output = kp*error;
38.
39. /*Find the direction of rotation for the wheels*/
40. bool direction;
41. if(output > 0)
42. {
43. direction = true;
44. }
45. else if(output < 0)
46. {
47. direction = false;
48. }
49.
50. /*clamp values to a maximum and a minimum*/
51. if(fabs(output) > MAX_SPEED)
52. {
53. output = MAX_SPEED;
54. }

7

55. else if(fabs(output) < MIN_SPEED)
56. {
57. output = MIN_SPEED;
58. }
59.
60. /*Move motors at specified velocity*/
61. motor_0_speed((int)output, direction);
62. motor_1_speed((int)output, direction);
63. }
64.

## Repeatable control loop

Finally, we want to make our control repeatable, meaning that we want to execute our control

## loop as many times as we wish. For this, we need to introduce an MIN_ERROR term that will serve as the absolute minimum error value that we are willing to tolerate. For example, a

MIN_ERROR equals to 10 means that we are willing to accept a minimum error of +-10 encoder

## counts. Ideally MIN_ERROR should be 0, but sometimes achieving this performance requires

longer correction time and/or more tuning. Our control algorithm will continuously correct its distance output until we achieve this minimum error tolerance.

Using the code below, you can see that the mouse will repeatedly try to achieve the target distance, then wait for a button press to repeat the process again.

1. #include <Encoder.h>
2. #include "micromouse.h"
3.
4. Encoder right_encoder(ENCODER_0_CHA, ENCODER_0_CHB);
5. Encoder left_encoder(ENCODER_1_CHA, ENCODER_1_CHB); 6.
7. const long int MAX_SPEED = 255;
8. const long int MIN_SPEED = 70;
9. const long int MIN_ERROR = 5;
10.
11. /*One cell distance is approximately 1090 encoder counts*/
12. long int target_distance = 1090;
13. /*Proportional gain coefficient*/
14. float kp = 1.0;
15.
16. void setup()
17. {
18. /*Initialize motors*/
19. motors_init();
20. /*Initialize serial console*/
21. Serial.begin(9600);
22. }
23.
24. void loop()
25. {
26. /*Wait for button press*/
27. while(digitalRead(BUTTON) != HIGH);
28. delay(1500);
29.
30. /*Keep running the control loop until the error is less that the
31. * minimum specified error (MIN_ERROR)
32. */
33. long int error;

8

34. do
35. {
36. /*Read encoder for left and right motors. Estimate
37. * mouse traveled distance by taking the average of
38. * both encoders.
39. */
40. long int r_count = right_encoder.read();
41. long int l_count = -left_encoder.read();
42. long int encoder_distance = (r_count + l_count) / 2; 43.
44. /*Distance control loop*/
45. /*Compute error*/
46. error = target_distance - encoder_distance;
47. /*Proportional action*/
48. float output = kp*error;
49.
50. /*Find the direction of rotation for the wheels*/
51. bool direction;
52. if(output > 0)
53. {
54. direction = true;
55. }
56. else if(output < 0)
57. {
58. direction = false;
59. }
60.
61. /*clamp values to a maximum and a minimum*/
62. if(fabs(output) > MAX_SPEED)
63. {
64. output = MAX_SPEED;
65. }
66. else if(fabs(output) < MIN_SPEED)
67. {
68. output = MIN_SPEED;
69. }
70.
71. /*Move motors at specified velocity*/
72. motor_0_speed((int)output, direction);
73. motor_1_speed((int)output, direction);
74. delay(20);
75. }while(abs(error) > MIN_ERROR);
76.
77. /*Stop both motors*/
78. motor_0_speed(0, true);
79. motor_1_speed(0, true); 80.
81. /*Reset encoders*/
82. right_encoder.write(0);
83. left_encoder.write(0);
84. }
85.

9

## Exercise:

## Using the code above, write a function for the control loop that follows this prototype:

1. void control_forward(int max_speed)
2. {
3. /*Put your control loop code here*/
4. }

## Put this function on your micromouse.h and micromouse.cpp files. We will be expanding and

using this function in the future.

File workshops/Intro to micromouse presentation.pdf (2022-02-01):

## IEEE UTEP Micromouse

# Micromouse Week 1

Introduction to IEEE UTEP Micromouse

## IEEE UTEP Micromouse

## Agenda for week 1

- Introduction to UTEP IEEE branch micromouse project
- Know your micromouse kit
- Technical background needed
- Roadmap for micromouse
- Software requirements for micromouse
- Teams for micromouse
- Weekly meetings

## IEEE UTEP Micromouse

## Micromouse IEE UTEP introduction

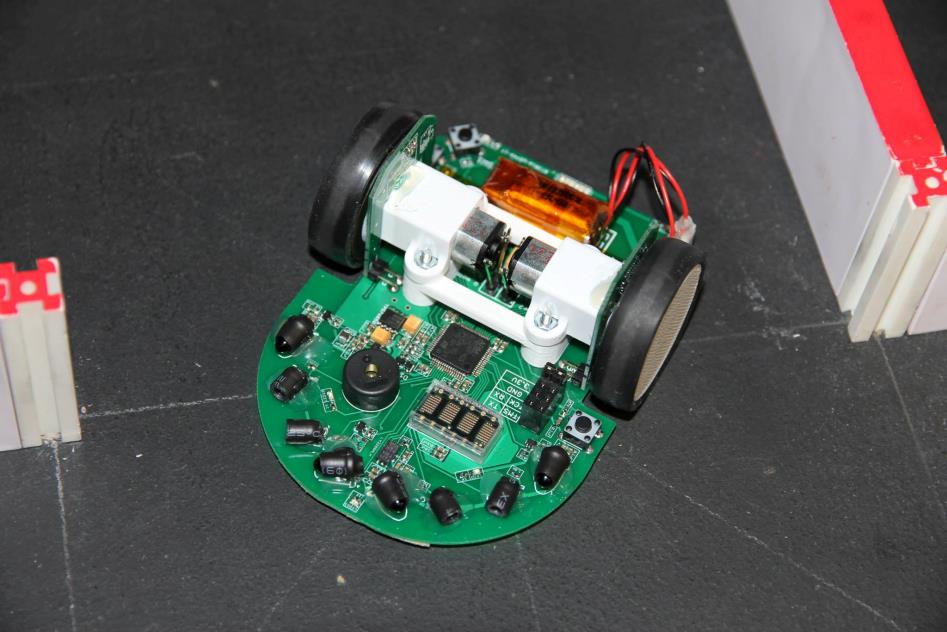
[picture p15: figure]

- Design a robotic mouse that can find the center of a maze in the shortest amount of time possible
- Place the mouse at the edge of the maze and let it run autonomously
- No human intervention and no hardcoded path!

## IEEE UTEP Micromouse

## Maze details

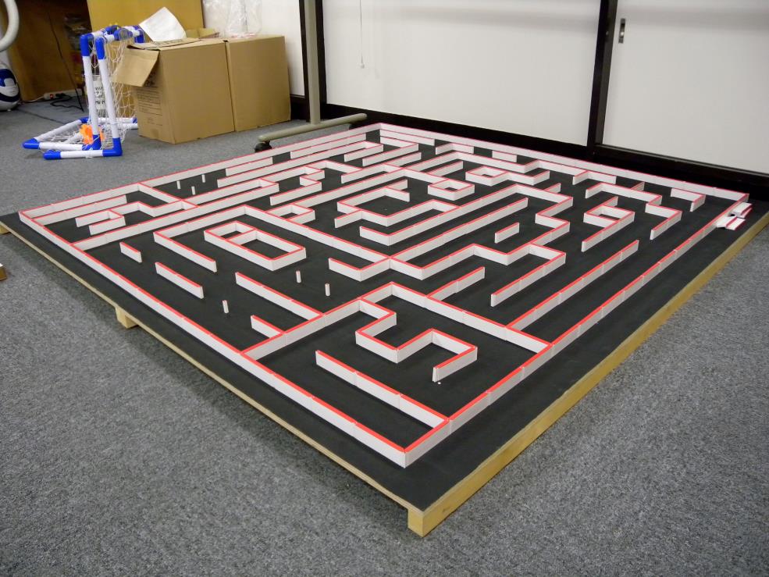
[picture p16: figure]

- 16x16 grid cells maze dimensions
- Each cell is 180mm square
- Walls are 50mm high
- Random maze
- Mouse should not knock, jump or attempt to destroy any walls
- We only have a half micromouse maze

## IEEE UTEP Micromouse

## Know your micromouse kit

- 4 IR LED proximity sensors
- Arduino Nano
- L293D DC motor drive

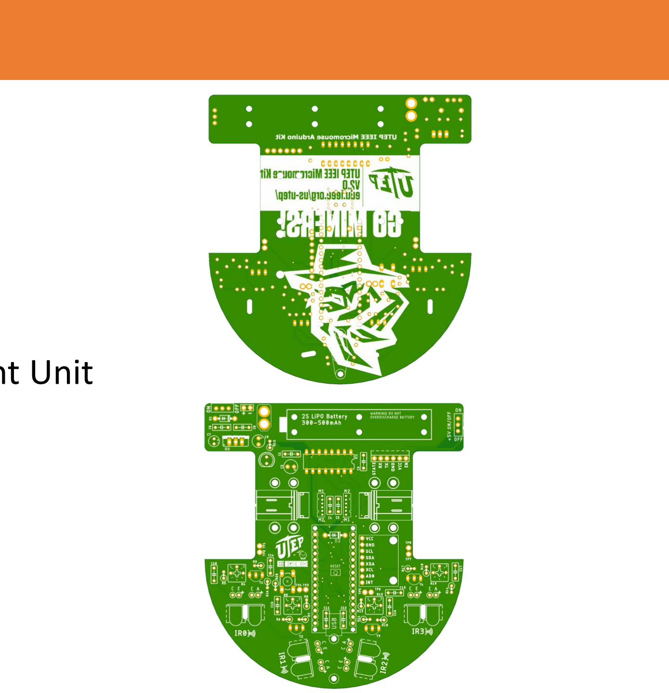
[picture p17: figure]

- MPU6050 Inertial Measurement Unit (IMU)
- Battery Power supply
- Hall effect encoders
- HC-05 Bluetooth (optional)

## IEEE UTEP Micromouse

## More about your kit

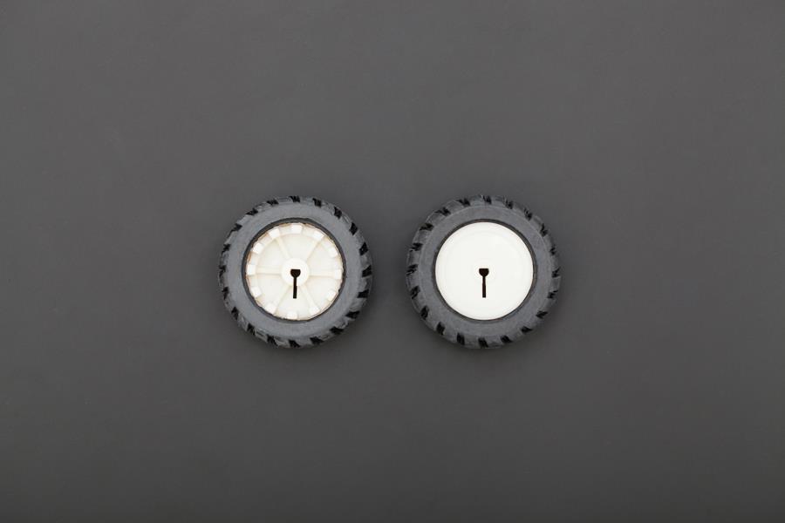
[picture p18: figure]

- DC motors with JST SM connectors (Fully modular)
- 30:1 gearbox, 310 RPM
- 42x19mm wheels
- All components are attached to the PCB
- The PCB is the mouse!
- You get to keep the PCB! (Not including the motors, battery and Bluetooth)

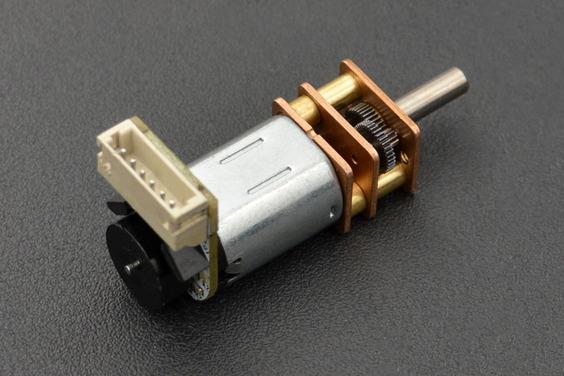
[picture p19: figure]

## IEEE UTEP Micromouse

## Micromouse technical background

- Wall detection using IR LEDs
- DC motor control
- Position control using hall effect encoders
- Angular displacement control using gyroscopes
- Path finding
- Systems control engineering

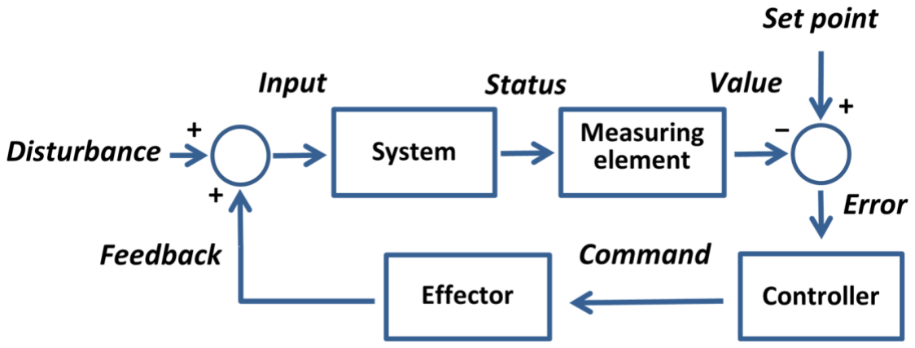
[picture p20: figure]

## IEEE UTEP Micromouse

## Roadmap to micromouse

1. DC motor control using pulse width modulation
2. Encoder for position feedback
3. Wall detection using IR LEDs
4. Cell exploration using dc motor control and wall detection, forward/backward
5. Measure yaw angular displacement using a gyroscope
6. Cell exploration using dc motor control, wall detection and gyroscopes
7. Path finding algoritm to find the center of the maze
8. Optimize cell exploration speed
9. Design your own micromouse hardware from scratch (if we have time)

## IEEE UTEP Micromouse

## Software requirements

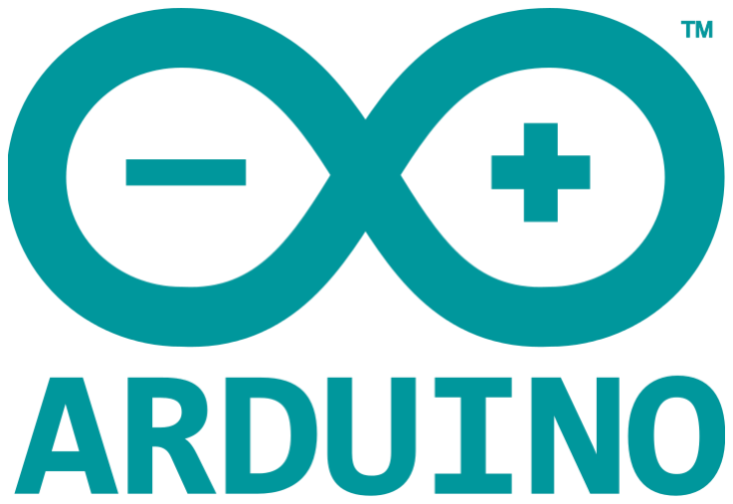
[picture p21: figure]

- We will be using the Arduino IDE
- Entirely written C/C++
- No required experience in any language

## IEEE UTEP Micromouse

## Let’s get into teams!

- 3-5 people teams
- Mix of grade classification is encouraged but not required

## IEEE UTEP Micromouse

## Weekly meetings

- Open meetings to work on micromouse every Friday from 1:00 PM to 3:00 PM
- Work on micromouse at your own pace
- Every meeting will have a new topic
- We will try to stick to the roadmap shown previously
- Handouts/presentations will be given if needed

## IEEE UTEP Micromouse

## What is next?

- Next meeting will be on 10/15 from 1:00PM to 3:00PM
- Get you micromouse kit
- Micromouse soldering workshop

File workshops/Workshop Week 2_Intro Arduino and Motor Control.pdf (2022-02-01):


# Workshop Week 2: Intro to Arduino and motor control

2

Objective:

Start coding with Arduino and learn the structure of an Arduino sketch, C programming syntax, digital input/output and motor control using the L293D dual H-bridge.
Background Information:

Today you and your teammates will get to code your first Arduino program/sketch! But before that, let’s go over what and Arduino is, what can it do and how we are going to use it to solve a maze.

An Arduino is basically a tiny computer that accepts low level commands to control hardware such as DC motors, LEDs, encoders, etc. What sets an Arduino apart from a general-purpose computer is its ability to start a program almost immediately and respond to signal events in a matter of microseconds (sometimes even nanoseconds). This is important to control critical hardware processes with strict timing. A few examples are a computer mouse, computer keyboard, engine control units, home refrigeration, handled gaming devices and medical devices. You will often hear the term “embedded device” or “embedded system” when it comes to Arduinos and other similar platforms, this term is used because these devices are often “hidden” away inside everyday electronics where it might not be obvious that a computer is controlling the whole show!

So, what makes an Arduino so popular? Well, its simplicity to use! Microcontroller/embedded devices usually have a steep learning curve, and Arduino tries to lower the gap for entry level programmers, such as yourself! Now, to solve the maze using the Arduino, we must learn the structure of an Arduino sketch and some C programming. Some of the code might look complicated and intricate, but we will explain it as we go, and after some practice, you will start to see patterns in the software you write. Don’t be scared by not knowing or having little practice with C, we will teach the basics and after a few workshops you will get good at C! Let’s get started

3

Arduino Sketch:

First thing you must learn is the basic structure of an Arduino sketch. If you open an Arduino sketch you will see the following two functions.

1. void setup() {
2. // put your setup code here, to run once: 3.
4. }
5.
6. void loop() {
7. // put your main code here, to run repeatedly: 8.
9. }

Since we are dealing with C programming, we must explain some syntax to you:

1. A function in C is a way to organize code into functional blocks. Using a function allows you to run the same piece of code several times without having to write the same code again. Furthermore, you might think of a function as an extension to a mathematical expression y = f(x), where x is the input and y the output. In C, the input can be a variety of data types and it is not only limited to integers or fractions. Here is the syntax for a function in C that takes 2 integers as its arguments and returns the sum of these 2 integers. To use a function first you must declare what the function does, then you call the function so that it runs the code inside the curly brackets.
1. // A function that returns the sum of 2 integers
2. // A function has void as its input or output will not accept or return anything
3. // First define the function does and what is name is
4. int add(int a, int b)
5. {
6. return a + b;
7. }
8.
9. void loop()
10. {
11. //call your addition function and store the value in a variable
12. int sum = add(1, 2)
13. }
2. A comment in C can be expressed in 2 ways
1. // This is a comment. A comment is useful to explain your code
2.
3. /* This is a multiline comment. Use this format when you must explain your code in detail
4. and your explanation will span several lines of text
5. */
6.

4

3. Variables in C express the data type that you are using and virtually every sketch has them. Variables, as the names implies, can change its value at any point in the program. This is true unless you declare the variable as a constant with the keyword const. There are several datatypes such as int, float, char, double, long and others. Variables are useful when you need a global value that will change often in your program or when you want to save the result from the output of a function.
1. int integer = 10; /*This is an integer datatype; you declare the datatype then the name of the variable and optionally an assignment. In this case we assign the value 10 to a variable with the name ‘integer’*
2.
3. float fraction = 3.1415; //This is a float datatype,
4. char character = ‘a’; //This is a character datatype

Ok with that out of the way, lets dive into the 2 functions inside your Arduino sketch

1. void setup() {
2. // put your setup code here, to run once:
3.
4. }

The setup function will be called by the Arduino when you first apply power or hit the reset button. You must define what the setup function does. This function is used to initialize all the pins that are going to be used.

1. void loop() {
2. // put your main code here, to run repeatedly: 3.
4. }

The loop function will be called continuously by the Arduino AFTER the setup function has finished executing its instructions. The loop function will execute all the code inside the curly brackets line by line in order. Once it reaches the end, the loop function will go back to the beginning to execute the same code again. This is where you place all your ‘useful’ code, or the code that runs the main algorithm.

Just to give you a taste on what this loop will look like once we finish the micromouse, below is the pseudo code (https://en.wikipedia.org/wiki/Pseudocode) for the complete micromouse algorithm inside the loop function

5

1. /*Micromouse algorithm to solve an unknown maze*/
2. void loop()
3. {
4. //while mouse is not on the center cell
5. //scan for walls
6. //add walls to the maze
7. //run path finding algorithm (flood fill)
8. //Find best neighbor (neighbor with lowest value)
9. //Turn towards best neighbor
10. //Move forward
11. //Found center of the maze!
12. }
13.

Arduino functions for digital input/outputs

Next, we must learn how to control digital hardware. To be more specific, we must know how to setup digital input/outputs, read digital inputs, and write to digital outputs. On your micromouse board, you will find a button next to the Arduino. Let’s set it up as a digital input, read its value and store it in a variable.

1. #include “micromouse.h”
2.
3. void setup() {
4. // put your setup code here, to run once:
5. | pinMode(BUTTON, INPUT); | //Set button pin as input
6. }
7.
8. void loop() {
9. // put your main code here, to run repeatedly:
10. int value = digitalRead(BUTTON);
11. }

Ok cool, we can read a digital input, but what can we do with this? Let’s experiment with a digital output. Let’s set up a digital output that will light up the onboard LED on the Arduino.

1. #include "micromouse.h"
2.
3. void setup() {
4. // put your setup code here, to run once:
5. pinMode(USER_LED, OUTPUT);
6. pinMode(BUTTON, INPUT);
7. }
8.
9. void loop() {
10. // put your main code here, to run repeatedly:
11. int value = digitalRead(BUTTON);
12. }
13.

6

Then let’s use a conditional statements (https://www.guru99.com/c-if-else-statement.html) to know whether the button was pressed or not. If it was pressed light up the LED, if it was not, then turn it off.

1. #include "micromouse.h"
2.
3. void setup() {
4. // put your setup code here, to run once:
5. pinMode(USER_LED, OUTPUT);
6. pinMode(BUTTON, INPUT);
7. }
8.
9. void loop() {
10. // put your main code here, to run repeatedly:
11. int value = digitalRead(BUTTON);
12.
13. if(value == HIGH)
14. {
15. digitalWrite(USER_LED, HIGH);
16. }
17. else
18. {
19. digitalWrite(USER_LED, LOW);
20. }
21. }
22.

The only new syntax that you see on the previous code is the if and else statement, so let’s go over it.

5. The if statement checks whether a statement is true or false. If it is true, then code inside the curly brackets will execute, if IT IS NOT true, then the code inside the else’s statement curly brackets will execute. In the above example we are checking whether the variable ‘value’ is HIGH (button was pressed) or else (button was not pressed). Motor control and AnalogWrite

Now we are ready to do more advanced stuff! We are going to control DC motors using 5 pins from the Arduino. These signals will control the speed and direction of the motors individually. We know that we must setup these pins as outputs, so let’s do that inside the setup function

1. #include "micromouse.h"
2. void setup() {
3. /*Setup motor pins*/
4. pinMode(ENABLE, OUTPUT);
5. pinMode(MOTOR_0_1A, OUTPUT);
6. pinMode(MOTOR_0_2A, OUTPUT);
7. pinMode(MOTOR_1_1A, OUTPUT);
8. pinMode(MOTOR_1_2A, OUTPUT);
9. }
10.
11. void loop() {
12. }

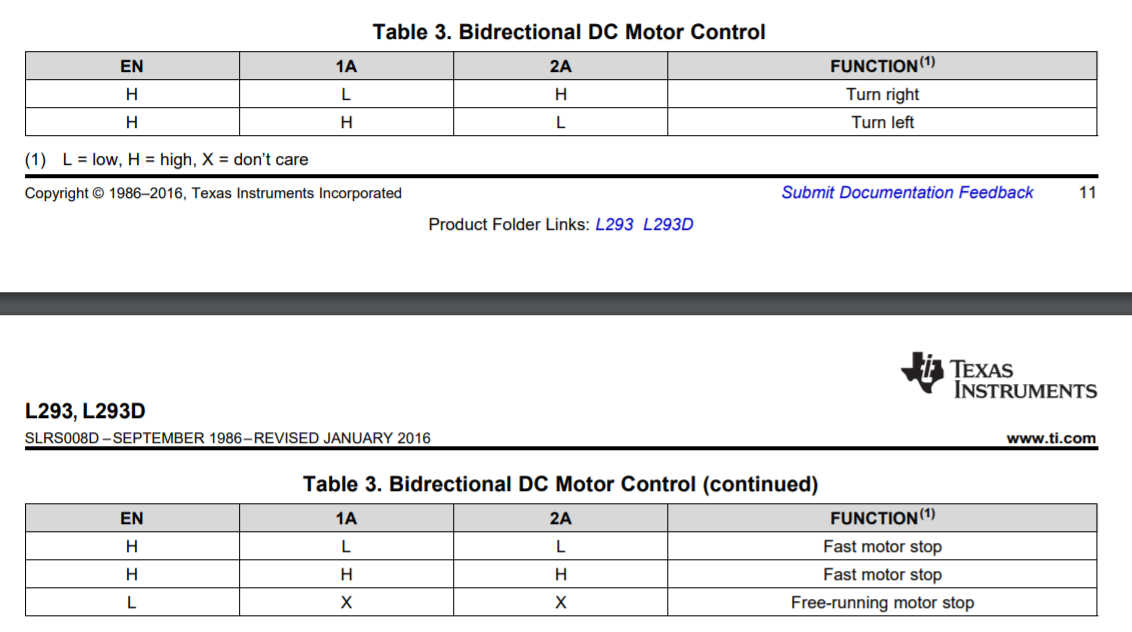
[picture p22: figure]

7

To control the motor direction and velocity, we are going to use the following truth table for the L293D (https://www.ti.com/lit/ds/symlink/l293.pdf) chip.

In the table you can see that applying a HIGH to Enable, LOW to 1A and HIGH to 2A will turn the motor right. The motor will turn left if Enable is HIGH, 1A is HIGH and 2A is LOW. Finally, the motor will stop if either Enable is LOW, or if both 1A and 2A are LOW. Using this table, we can make the mouse move forward, backwards, left or right by simply changing the order of the signal values. To make this more interesting, let’s also add user input with the button.

1. #include "micromouse.h"
2.
3. const int speed = 64;
4.
5. void setup() {
6. /*Setup motor pins*/
7. pinMode(ENABLE, OUTPUT);
8. pinMode(MOTOR_0_1A, OUTPUT);
9. pinMode(MOTOR_0_2A, OUTPUT);
10. pinMode(MOTOR_1_1A, OUTPUT);
11. pinMode(MOTOR_1_2A, OUTPUT); 12.
13. /*Setup button pin*/
14. pinMode(BUTTON, INPUT);
15. }
16.
17. void loop() {
18. /*Wait for user input*/
19. while(digitalRead(BUTTON) != HIGH)
20. {
21.
22. }
23. delay(1000);
24.

8

25. /*Forward*******************************/
26. analogWrite(MOTOR_0_1A, 0);
27. analogWrite(MOTOR_0_2A, speed);
28.
29. analogWrite(MOTOR_1_1A, speed);
30. analogWrite(MOTOR_1_2A, 0);
31. }

On the previous code, there are 3 things that stand out. First, we have

1. while(digitalRead(BUTTON) != HIGH)
2. {
3.
4. }

this introduces a new C syntax instruction, the while loop statement. This instruction will execute the code inside the curly brackets UNTIL the condition is met. In this case we are constantly asking if the user has pressed the button or to put it simply, do nothing WHILE the BUTTON IS NOT HIGH.

Another interesting piece of code is line 3.

1. const int speed = 64;

Here, we are declaring a variable named speed that will be visible to all portions of the Arduino sketch. Notice that we are declaring this variable as const since we are not planning to change this variable once the program starts.

Declaring global variables like this can be useful when several portions of your program use the same value. If the value changes in the future, all references to that variable will change as well. So, for the example above, you only must change the global ‘speed’ variable to modify the speed in which the mouse moves.

Lastly, on line 23, we have the function

1. delay(1000)

This will simply delay execution of the next instruction by 1000 milliseconds or 1 second

9

Exercise:

Now is your turn to write some code and start practicing with C. Using the code template below implement the following algorithm at the WRITE YOUR OWN CODE comment

1. /*This micromouse workshop will teach you:
2. * 1. Arduino sketch structure
3. * 2. Basic C syntax
4. * 3. Digital input output
5. * 4. Motor driver truth table
6. * 5. Driving forward/ backwards, turning left/right
7. *
8. *
9. * L293D dual h-bridge datasheet https://www.ti.com/lit/ds/symlink/l293.pdf
10. *
11. * Bidirectional motor control page 11-12
12. * ENABLE | | | MOTORx_1A | | | MOTORx_2A | | | FUNCTION
13. * ----------------------------------------------------------------------------------
14. * HIGH | | | LOW | | | HIGH | | | Turn right
15. * HIGH | | | HIGH | | | LOW | | | Turn left
16. * HIGH | | | LOW | | | LOW | | | Fast motor stop
17. * LOW | | | X | | | X | | | Free-running motor stop
18. *
19. * MOTORx_1A and MOTORx_2A can be replaced with PWM signals to control the velocity of the motor
20. */
21.
22. #include "micromouse.h" 23.
24. const int speed = 64;
25.
26. void setup() {
27. /*Setup motor pins*/
28. pinMode(ENABLE, OUTPUT);
29. pinMode(MOTOR_0_1A, OUTPUT);
30. pinMode(MOTOR_0_2A, OUTPUT);
31. pinMode(MOTOR_1_1A, OUTPUT);
32. pinMode(MOTOR_1_2A, OUTPUT); 33.
34. /*Setup button pin*/
35. pinMode(BUTTON, INPUT);
36. }
37.
38. void loop() {
39. /*Wait for user input*/
40. while(digitalRead(BUTTON) != HIGH);
41. /*Delay 1000 milliseconds*/
42. delay(1000);
43.
44. /*Forward*/
45. analogWrite(MOTOR_0_1A, 0);
46. analogWrite(MOTOR_0_2A, speed); 47.
48. analogWrite(MOTOR_1_1A, speed);
49. analogWrite(MOTOR_1_2A, 0); 50.
51. /*Delay 1000 milliseconds*/
52. delay(1000);
53.
54. /*Stop*/
55. analogWrite(MOTOR_0_1A, 0);
56. analogWrite(MOTOR_0_2A, 0);

10

57.
58. analogWrite(MOTOR_1_1A, 0);
59. analogWrite(MOTOR_1_2A, 0);
60.
61. /******WRITE YOUR OWN CODE*******/
62. /*Wait for user input*/
63.
64. /*Delay 1000 milliseconds*/
65.
66. /*Backward*/
67.
68. /*Delay 1000 milliseconds 69.
70. /*Stop*/
71.
72. /*Wait for user input*/ 73.
74. /*Delay 1000 milliseconds*/ 75.
76. /*Turn right*/
77.
78. /*Delay 1000 milliseconds 79.
80. /*Stop*/
81.
82. /*Wait for user input*/ 83.
84. /*Delay 1000 milliseconds*/ 85.
86. /*Turn left*/
87.
88. /*Delay 1000 milliseconds 89.
90. /*Stop*/
91. }

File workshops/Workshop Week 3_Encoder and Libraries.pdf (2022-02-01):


# Workshop Week 3: Encoders and Arduino Libraries

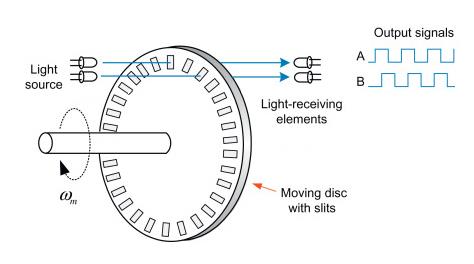
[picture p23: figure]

2

Objective:

Learn how an encoder works and how to use it to go from angular translation to linear translation. Learn how to download and use new Arduino libraries.
Background Information:

One of the things that the mouse must do is move a specified distance accurately. From last week, you know that you can control the speed in which the mouse moves, but you cannot tell how far you moved on a given time interval. To know this, you must use some type of sensor, and for the micromouse this sensor is an encoder. So, what is an encoder? An encoder is a sensor that triggers voltage pulses at specific angle intervals. The encoder does this by using a photo interrupter or a hall effect sensor. Figures 1 and 2 show how this works on a mechanical level. But how does this translate to motion and direction? Well to know how much the wheel has rotated, you only need to count the number of pulses. For the direction, you need to know which channel signal is leading and which is lagging. In figure 1 and 2 you can see that the signals are always out of phase, or misaligned. On figure 3 you can observe how this misalignment identify the direction in which wheel encoder is moving by reading the value of the opposite signal channel on the encoder.

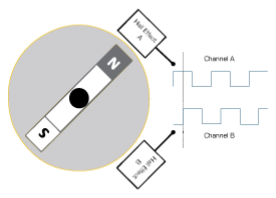
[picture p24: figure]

Figure 1 Hall effect encoder | Figure 2 Photo interrupter encoder

3

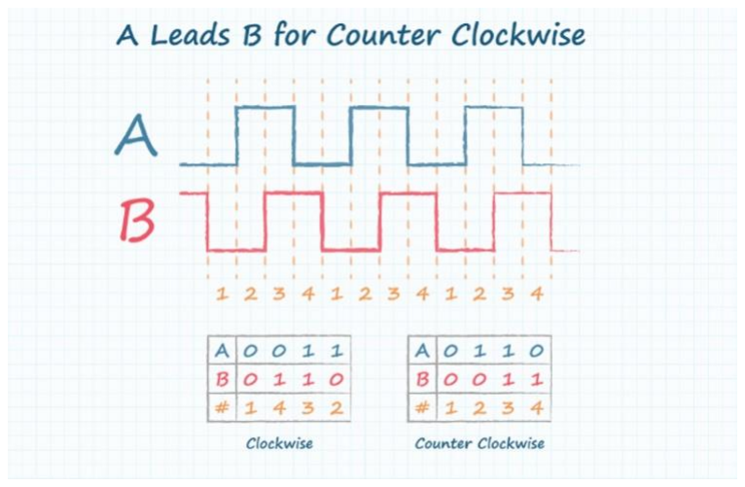
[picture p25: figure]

Downloading and using Arduino Libraries

One of the reasons why Arduino is so popular is because of the number of libraries that it has. If you have a gadget or device that you want to control, the Arduino community most likely has a library for it. For the micromouse we will use an encoder library to setup and read the value from both motor encoders. The steps to download the encoder library are:

1. In an Arduino sketch go to Sketch/Include Libraries/Manage Libraries or press CTRL+SHIFT+I

Figure 3 Pulse order for clockwise and counterclockwise encoder signals


4

2. On the new window, on the search bar type Encoder and look for the Encoder library by Paul Stofreggen


3. Click on the install button. Let it download, once it’s finished you can start using the library on all your micromouse sketches

To use this library, open a new micromouse Arduino sketch (sketch on last week’s email) and write the following code:

1. /*This micromouse workshop will teach you:
2. * 1. Downloading Arduino libraries
3. * 2. Encoders for position and speed
4. */
5.
6. #include "micromouse.h"
7. #include <Encoder.h>
8.
9. Encoder right_encoder(ENCODER_0_CHA, ENCODER_0_CHB);
10. Encoder left_encoder(ENCODER_1_CHB, ENCODER_1_CHA); 11.
12. void setup()
13. {
14.
15. }
16.
17. void loop()
18. {
19.
20. }
21.

Compile and verify that your code has no errors. If Arduino does not throw any compilation errors, then you are set! You have now downloaded and used your first Arduino library, wasn’t that easy?

5

Using encoders for linear displacement

Now that we can use the encoder library, let’s use it to measure the linear displacement of the mouse. The first thing that we need to address is the relationship between angular and linear displacement. Remember that the encoder only measures angular displacement in the form of pulse counts. The second thing to consider is how to relate pulse count to angular displacement. In the end, we want to end up with a relationship that takes as an input the distance we want to travel in millimeters, and then output the encoder count we must have to travel that distance.

Linear Displacement → Angular Displacement → Encoder Pulse count

The relationship between the angular and linear displacement is given by the following equation

x = 2πr

Where x is the total distance travelled and r is the radius of the wheel. The radius of the wheel is r = 21mm. For example, in one full rotation of the wheel, we will displace the mouse a distance of x = 2(21mm)π = 131.94mm.

Now we need to relate the encoder pulses to angular displacement. To do this, we first need to know the pulse count in one wheel revolution. For the motors we are using this value is 800 counts/rev.

We can use this fact to come up with the following equation:

c(x) = (

x
131.94)(800)

Where c is the encoder pulse count and x is the desired distance for the mouse. For example, on the micromouse competition it is required that the mouse moves in “steps” of 180 millimeters, using the above equation, we can know how many encoders pulses we need to count until we reach the desired 180-millimeter distance c(180) = (

180
131.94) (800) = 1091.4 ≃

1091 pulses

Last thing to consider is that we can use both encoders and average their values to measure distance. This will help smoothing any fluctuations we might have on one of the motors at any given time.

Enough theory! Let’s write some code!

6

1. /*This micromouse workshop will teach you:
2. * 1. Downloading Arduino libraries
3. * 2. Encoders for position and speed
4. */
5. #include "micromouse.h"
6. #include <Encoder.h>
7.
8. Encoder right_encoder(ENCODER_0_CHA, ENCODER_0_CHB);
9. Encoder left_encoder(ENCODER_1_CHB, ENCODER_1_CHA); 10.
11. const int speed = 64;
12.
13. void setup()
14. {
15. /*Setup motor pins*/
16. pinMode(ENABLE, OUTPUT);
17. pinMode(MOTOR_0_1A, OUTPUT);
18. pinMode(MOTOR_0_2A, OUTPUT);
19. pinMode(MOTOR_1_1A, OUTPUT);
20. pinMode(MOTOR_1_2A, OUTPUT); 21.
22. pinMode(BUTTON, INPUT);
23. Serial.begin(9600);
24. }
25.
26. void loop()
27. {
28.
29. /*Move motor forward at given speed*/
30.
31. /*Forward distance to travel 1 cell is 180mm
32. * 1 rev = 720 encoder counts, so (counts/rev) = 800.
33. * Linear distance travelled on 1 wheel revolution is given
34. * by x = 2*r*pi
35. * where r = wheel radius
36. | * | x = linear distance
37. *
38. * so x = 2*21*pi = 131.946mm
39. *
40. * To generalized
41. * (x/131.946) * 800 = c
42. * where x = desired distance and c = pulse count
43. * counts/rev = encoder counts in one wheel revolution
44. * (180mm/131.946mm) * 800 = 1091.4 ~= 1091
45. */
46. long int right_encoder_count;
47. long int left_encoder_count;
48. long int average_encoder_count = 0;
49.
50. right_encoder_count = right_encoder.read();
51. left_encoder_count = -left_encoder.read(); //This should be negative! This encoder drives the opposite way
52. average_encoder_count = (right_encoder_count + left_encoder_count)/2;
53.
54. /*print values to serial console*/
55. Serial.print(right_encoder_count);
56. Serial.print(“, ”);
57. Serial.print(left_encoder_count);
58. Serial.print(“, ”);
59. Serial.println(average_encoder_count); 60.
61. /*Stop motors*/
62.
63. }

7

To see the values of the left, right and average encoder count, open the Serial Monitor on Arduino


And select 9600 for the baud rate


After connecting and uploading the code to your Arduino, you will see data streaming to the console giving you the value of the left, right and average encoder count values. In future workshops we will discuss more in detail the serial console and how to use it in Arduino sketches, for now all you need to know is that the values will be printed to this console. Try to verify that one revolution matches the value of 800 count/rev. For the wheels of your mouse, this might be different although we don’t think it will be by much.

8

Activity

Now is your turn to work on the micromouse. Using the information on encoders and the template code below, have your micromouse traverse 180mm forward, stop and then reset the encoder value back to zero. Try and measure the traveled distance of the mouse using a ruler or a measured piece of tape.

1. /*This micromouse workshop will teach you:
2. * 1. Downloading Arduino libraries
3. * 2. Encoders for position and speed
4. */
5.
6. #include "micromouse.h"
7. #include <Encoder.h>
8.
9. Encoder right_encoder(ENCODER_0_CHA, ENCODER_0_CHB);
10. Encoder left_encoder(ENCODER_1_CHB, ENCODER_1_CHA); 11.
12. const int speed = 64;
13.
14. void setup()
15. {
16. /*Setup motor pins*/
17. pinMode(ENABLE, OUTPUT);
18. pinMode(MOTOR_0_1A, OUTPUT);
19. pinMode(MOTOR_0_2A, OUTPUT);
20. pinMode(MOTOR_1_1A, OUTPUT);
21. pinMode(MOTOR_1_2A, OUTPUT); 22.
23. pinMode(BUTTON, INPUT);
24. }
25.
26. void loop()
27. {
28. /*Wait for user input*/
29. while(digitalRead(BUTTON) != HIGH);
30. delay(1000);
31.
32. /*Move both motors forward at given speed*/
33. analogWrite(MOTOR_0_1A, 0);
34. analogWrite(MOTOR_0_2A, speed);
35.
36. analogWrite(MOTOR_1_1A, speed);
37. analogWrite(MOTOR_1_2A, 0); 38.
39. long int right_encoder_count;
40. long int left_encoder_count;
41. long int average_encoder_count = 0;
42.
43. /*while distance != 180mm, keep measuring encoders and running the motors*/
44. right_encoder_count = right_encoder.read();
45. left_encoder_count = -left_encoder.read();
46. average_encoder_count = (right_encoder_count + left_encoder_count)/2;
47. delay(20);
48.
49. /*Stop motors after you reach your destination*/
50.
51. /*Reset encoders*/
52. }
53.

9

Extra Activity

Using the code above, have your mouse move forward 180mm and then go back to its original position. This is going to require for you to reset the encoders (https://github.com/PaulStoffregen/Encoder/blob/master/Encoder.h)

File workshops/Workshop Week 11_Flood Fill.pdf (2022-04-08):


# Workshop Week 11: Flood Fill

2

Objective:

Understand what the maze coordinates and values are. Use the values of the maze cells to perform path planning using flood fill. Understand what variable pointers in the C programming language are, and why we would want to use them
Background information:

Last week we learned the basics on how to represent a maze and a mouse inside the Arduino’s memory. We also learned that we could visualize the maze and mouse by printing the output into a serial terminal. In today’s workshop, we will learn how to use the maze and mouse software to run the flood fill algorithm and find the shortest path to the center of the maze.

We will be using the well-known flood fill algorithm to find the center of the maze. Flood fill was initially used in computer graphics to fill bounded sections with a given color. If you ever used the bucket tool in paint, you know what the algorithm does. People discovered that the same algorithm could be used to compute distances from one cell to another, and they used it to quickly recompute cell values whenever they did not agree with the map (wall in between cells).

Later, it was found that the flood fill algorithm did not have to be run on every maze cell, and it only needed to be run when the current cell is one less than the lowest valued open neighbor. This dramatically increased the speed in which the mouse could find a valid path, so this is the algorithm that most micromouse enthusiasts use.

Here is the pseudo-code for the flood fill algorithm:

1. void flood_fill(int x, int y)
2. {
3. /*1. Push the current cell location into a stack*/
4.
5. /*2. Repeat the following until the stack is not empty*/ 6.
7. /*a. Pop a cell from the top of the stack*/
8. /*b. Find the minimum open neighbor value*/
9. /*c. If the minimum open neighbor value is not equal to the current cell value -1*/
10. /*i. Replace current cell value with minimum open neighbor value + 1*/
11. /*ii. Push all neighbors into the stack*/
12. }

This code might look daunting, but we are going to dissect it one chunk at a time. We are also going to be required to learn how to use a stack and C pointers. Ultimately, we will place our flood fill code inside the maze.cpp and maze.h source files, so that we can access it from our sketch

3

Maze Coordinates

Last workshop did not discuss the coordinate convention that the maze follows, so let’s address that in this section.

The maze coordinates are as follows:


Remember that the mouse position always starts at one of the maze corners, so you must make sure that your software reflects the initial position of the mouse
Maze cell values

The maze cell values tell you the number of moves we have left until we reach the center of the maze, or the target cell with value 0. For example, look at the maze below and see that every cell value tells you exactly how far, or how many moves you still have left in order to reach the 0-value cell


7 moves away

4 moves away

1 move away

4

You can see that by always moving towards the lowest cell value we can reach the center of the maze. In actual code, we will always have the mouse choose the open neighbor with the lowest cell value and move towards it. Pretty neat right?!
C Pointers and C structure pointers

Before tackling the flood fill algorithm, we need to get some new C functionality and syntax out of the way. First, the cells of the maze are represented as C data structures, which have the following syntax:

1. typedef struct
2. {
3. uint8_t value;
4. uint8_t pos;
5. uint8_t walls;
6. }cell_t;

A C data structure is nothing more than a collection of variables with an alias, in this case the alias is cell_t. The maze can now be represented as a 2-dimensional array of cells as follows:

1. cell_t maze[8][8];

Now, you might be thinking, why is this useful? Why would we ever want to use this? Well, the alternative is to declare multiple 2-dimensional arrays for the cell values, walls and position such as this:

1. uint8_t value[8][8]
2. uint8_t pos[8][8]
3. uint8_t walls[8][8]

Now we must worry about 2 more 2-dimensional arrays, which can lead to confusion and loss of meaning on what each array does. That is why something is useful to think in terms of C structures rather than individual variables.

For the next section, we need to access and modify the values of the cells. To do so we need to access its member variables. Because of the way the stack is designed, we need to understand how to access the structure members for a C pointer.

So, what is a C pointer? Basically, is a variable that stores the address of another variable. Now that sounds abstract, and the application of a C pointer is often not clearly explained, so allow us to explain how pointers are useful in this case.

For the maze, we already have the cells in memory by declaring the previous 8x8 cell array. For accessing a specific cell, we can do something like this:

1. cell_t current_cell = maze[0][0];

5

This is fine and it will work, but is not memory efficient, since the compiler will create a copy of the cell_t data structure, and that variable consumes 3 bytes of data (1 for value, 1 for walls and 1 for position). Now imagine that we have to push 100 cell_t into a software stack, that will consume 3 bytes * 100 = 300 bytes of memory. That is a lot for our tiny Arduino, which only has 2048 bytes of memory.

The alternative is to use a cell_t pointer variable as follows:

1. cell_t *current_cell = &maze[0][0];

Now this pointer only consumes 2 bytes of memory, so it goes without saying that this is an improvement from the previous implementation. Another thing to point out, is that the pointer memory size requirements will stay fixed at 2 bytes regardless of how big the data structure is.

To access the members of a C data structure pointer, we must write this code

1. cell_t *current_cell = &maze[0][0];
2. uint8_t value = current_cell->value;

Not so difficult right?
Software Stack

As you might have noticed, we are going to need a software stack to write the flood fill algorithm. A stack (https://www.tutorialspoint.com/data_structures_algorithms/stack_program_in_c.htm) is a data structure algorithm that performs Last In-First Out (LIFO) data access. For the sake of time, a software stack has been implemented for you to use in your flood fill software. You must update the micromouse workshop sketch (https://github.com/amartinezacosta/UTEP-IEEE-Micromouse/tree/main/code_template/micromouse_workshop_template) template to the latest version, or download the stack.cpp and stack.h files and place them inside your sketch.

To push a cell into the stack, use this code:

1. cell_t *current = &maze[0][0];
2. stack_push(current);

To pop a cell from the stack, use this code:

1. cell_t *current;
2. stack_pop(current);

6

Flood fill

With all that information out of the way, let’s tackle the flood fill algorithm. First let’s write a prototype function inside the maze.cpp file

1. /*FLOOD FILL CODE GOES HERE***************************************************/
2. void flood_fill(int x, int y)
3. {
4.
5. }
6. /*FLOOD FILL ENDS HERE********************************************************/

Next let’s fill out the function with some psudo-code and actual C code that we can start filling out:

1. /*FlOOD FILL CODE GOES HERE***************************************************/
2. void flood_fill(int x, int y)
3. {
4. /*Neighbor offsets for all orientations*/
5. int8_t neighbor_offset[4][2] =
6. {
7. {0, -1},
8. {1, 0},
9. {0, 1},
10. {-1, 0},
11. };
12.
13. /*Pointer to data structure.
14. See https://overiq.com/c-programming-101/pointer-to-a-structure-in-c/ */
15. cell_t *current;
16. cell_t *neighbor;
17.
18. /*Get current cell from maze. FILL THIS OUT*/ 19.
20.
21. /*Push current cell to the stack. FILL THIS OUT*/
22.
23.
24. /*Keep running until the stack is not empty. FILL THIS OUT*/
25. while()
26. {
27. /*Pop cell from the stack. FILL THIS OUT*/
28.
29. /*If this is the target cell (value 0), then break out of this loop. FILL THIS OUT*/ 30.
31. /*Get position from popped cell*/
32. uint8_t cx = GET_X_POS(current->pos);
33. uint8_t cy = GET_Y_POS(current->pos);
34.
35. /*Find the open neighbor with the lowest value*/
36. uint8_t minimum = 255;
37. for(int i = 0; i < 4; i++)
38. {
39. if((current->walls & (1 << i)) == 0)
40. {
41. /*Get neighborhs x and y coordinates*/
42. int8_t nx = cx + neighbor_offset[i][0];
43. int8_t ny = cy + neighbor_offset[i][1]; 44.

7

45. /*Get neighbor cell pointer from the maze*/
46. neighbor = maze_get_cell(nx, ny);
47. /*If the neighbor is less than the minimum,
48. * then set this cell value as the new minimum*/
49. if(neighbor->value < minimum)
50. {
51. /*FILL THIS OUT*/
52. }
53. }
54. }
55.
56. /*If the current cell value is not one less
57. * than the minimum ... FILL THIS OUT
58. */
59. if()
60. {
61. /*Increment the current cell value by the minimum + 1. FILL THIS OUT*/ 62.
63. /*Push all neighbors into the stack*/
64. for(int i = 0; i < 4; i++)
65. {
66. /*Get neighborhs x and y coordinates*/
67. int8_t nx = cx + neighbor_offset[i][0];
68. int8_t ny = cy + neighbor_offset[i][1]; 69.
70. /*Check that cell is not out of bounds*/
71. | if((nx > 0) | &&
72. (nx < (MAZE_WIDTH - 1)) &&
73. | (ny > 0) | &&
74. (ny < (MAZE_HEIGHT - 1)))
75. {
76. /*Get neighbor cell pointer from the maze*/ 77.
78.
79. if(neighbor->value != 0)
80. {
81. /*Push the neighbor into the stack if the value
82. * is not equal to 0. FILL THIS OUT*/
83.
84. }
85. }
86. }
87. }
88. }
89. }
90. /*FLOOD FILL ENDS HERE********************************************************/
91.

Your job now is to fill out the missing sections of the flood fill program so that it compiles cleanly. Then on your main sketch write this code to test your flood fill algorithm. The code will set up a test maze with walls and intial values. The intial values assume that there are no walls in between the cells, so it is the job of the flood fill algorithm to find the correct values given that are walls in between the cells.

1. #include "micromouse.h"
2. #include "maze.h"
3.
4. void setup()
5. {
6. /*Enable serial port for bluetooth*/
7. Serial.begin(9600);
8.
9. /*Initialize maze*/

8

10. maze_init(MAZE_WIDTH/2, MAZE_HEIGHT/2);
11. mouse_set_x(0);
12. mouse_set_y(MAZE_HEIGHT - 1);
13.
14. /*First column*/
15. maze_set_wall(0, 3, EAST);
16. maze_set_wall(0, 2, EAST);
17. maze_set_wall(0, 1, EAST); 18.
19. /*Second column*/
20. maze_set_wall(1, 3, EAST);
21. maze_set_wall(1, 2, EAST);
22. maze_set_wall(1, 1, EAST); 23.
24. /*Third column*/
25. maze_set_wall(2, 1, EAST);
26. maze_set_wall(2, 2, EAST);
27. maze_set_wall(2, 2, SOUTH);
28.
29. maze_print();
30. flood_fill(mouse_get_x(), mouse_get_y());
31. maze_print();
32. }
33.
34. void loop()
35. {
36. }
37.

Notice that you can run the flood fill algorithm in any cell on the maze. Play around with this function by passing different x and y values into your flood fill function. See how the maze values change according to the walls

9

Exercise:

Use the code from workshop 10 to move the mouse around the maze. Explore the maze several times so that the flood fill finds the values of the test maze so that it matches the values from the maze below


Figure 1 Final solved maze

Pseudo-code to explore and solve the maze

1. #include "micromouse.h"
2. #include "maze.h"
3.
4. void setup()
5. {
6. /*Enable serial port for bluetooth*/
7. Serial.begin(9600);
8.
9. /*Initialize maze*/
10. maze_init(MAZE_WIDTH/2, MAZE_HEIGHT/2);
11. mouse_set_x(0);
12. mouse_set_y(MAZE_HEIGHT - 1);
13.
14. /*First column*/
15. maze_set_wall(0, 3, EAST);
16. maze_set_wall(0, 2, EAST);
17. maze_set_wall(0, 1, EAST); 18.
19. /*Second column*/
20. maze_set_wall(1, 3, EAST);
21. maze_set_wall(1, 2, EAST);
22. maze_set_wall(1, 1, EAST); 23.
24. /*Third column*/
25. maze_set_wall(2, 1, EAST);
26. maze_set_wall(2, 2, EAST);
27. maze_set_wall(2, 2, SOUTH); 28.
29. maze_print();
30. }
31.
32. void loop()
33. {
34. /*Wait for key press*/

10

35. if(Serial.available() > 0)
36. {
37. /*Store key press*/
38. int c = Serial.read(); 39.
40. /*Run flood fill algorithm*/
41. /*Move mouse*/
42. /*Print maze*/
43.
44. }
45. }
46.

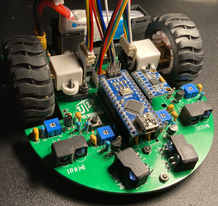
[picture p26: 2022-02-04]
img/micromouse_0.png

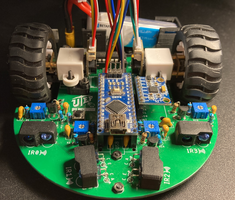
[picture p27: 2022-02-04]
img/micromouse_1.png

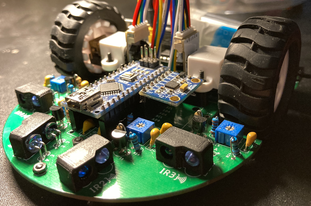
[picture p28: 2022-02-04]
img/micromouse_3.png

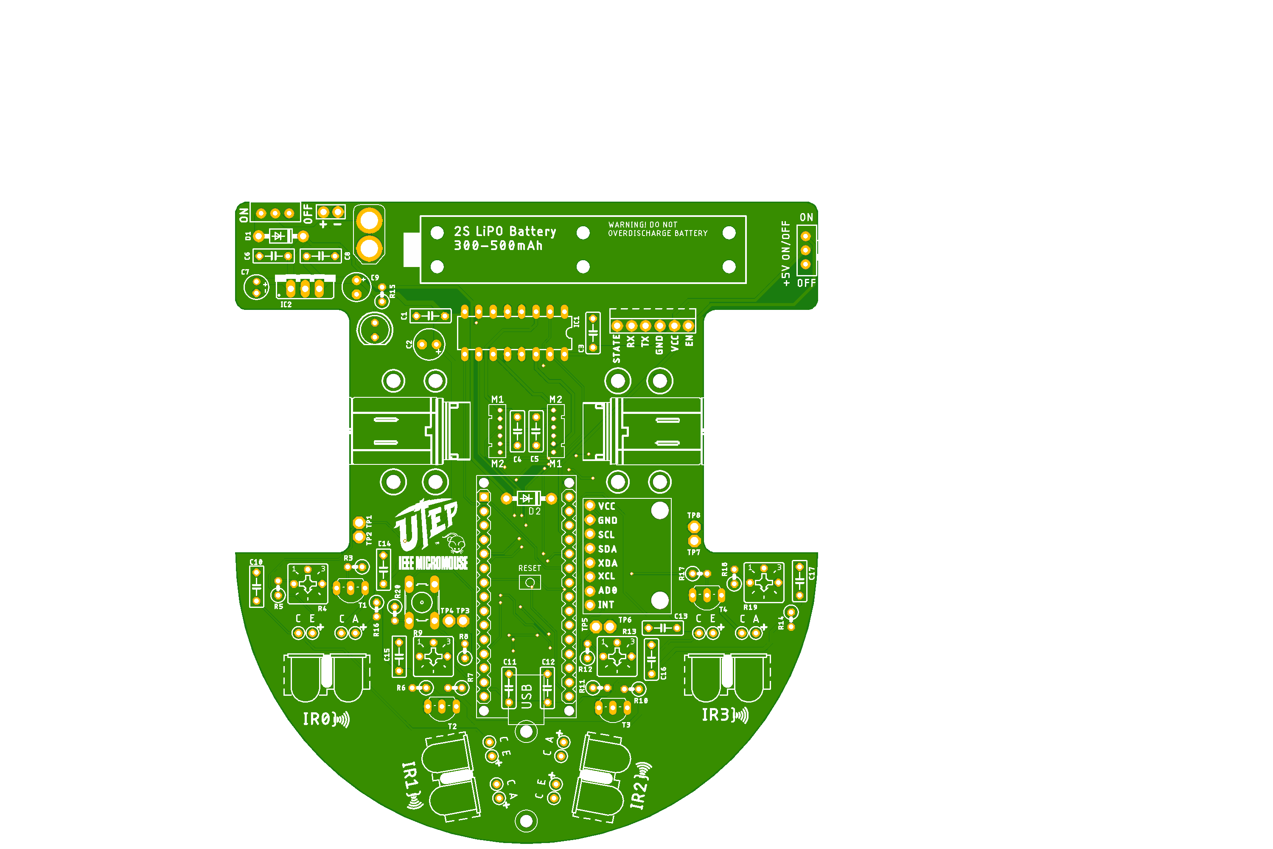
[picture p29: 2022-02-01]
micromouse_arduino_nano_kit/Micromouse Arduino Nano.png

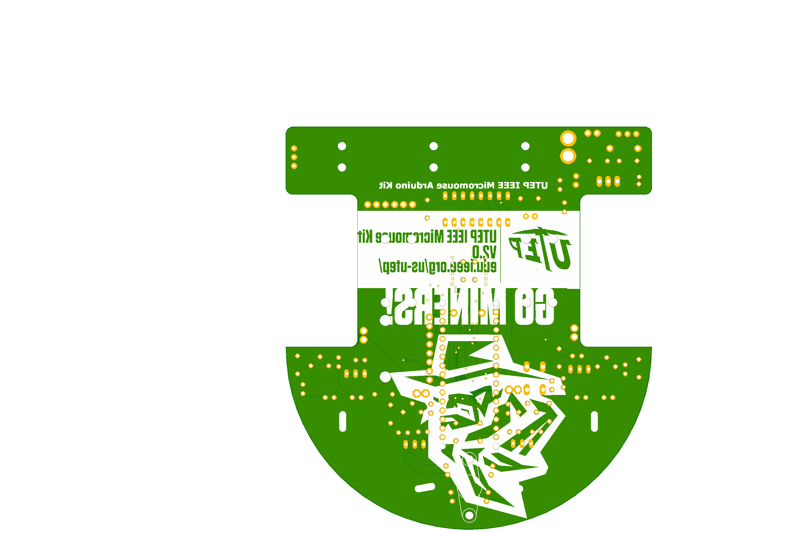
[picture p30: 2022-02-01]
micromouse_arduino_nano_kit/Micromouse Arduino Nano_bottom.png

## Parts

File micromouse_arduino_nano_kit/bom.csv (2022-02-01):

Qty | Value | Device | Package | Parts | Description
1 |  | 10-XX | B3F-10XX | S1 | OMRON SWITCH
4 |  | 2N4124-NPN-TO92-CBE | TO92-CBE | T1, T2, T3, T4 | NPN Transistror
1 |  | 78XXS | 78XXS | IC2 | VOLTAGE REGULATOR
1 |  | LED5MM | LED5MM | LED1 | LED
2 |  | SCHOTTKY-DIODEDO41-7 | DO41-7 | D1, D2 | Schottky Diode
9 | 0.1uF | C-EU050-025X075 | C050-025X075 | C1, C3, C4, C5, C8, C10, C11, C12, C13 | CAPACITOR, European symbol
1 | 0.33uF | C-EU050-025X075 | C050-025X075 | C6 | CAPACITOR, European symbol
4 | 10 | R-US_0207/2V | 0207/2V | R6, R10, R14, R16 | RESISTOR, American symbol
1 | 10k | R-US_0207/2V | 0207/2V | R20 | RESISTOR, American symbol
4 | 10k | TRIM_US-CT6 | CT6 | R4, R9, R13, R19 | POTENTIOMETER
4 | 10uF | C-EU050-025X075 | C050-025X075 | C14, C15, C16, C17 | CAPACITOR, European symbol
1 | 10uF | CPOL-USE2.5-5 | E2,5-5 | C9 | POLARIZED CAPACITOR, American symbol
4 | 1k | R-US_0207/2V | 0207/2V | R5, R8, R12, R18 | RESISTOR, American symbol
5 | 220 | R-US_0207/2V | 0207/2V | R3, R7, R11, R15, R17 | RESISTOR, American symbol
1 | 220uF | CPOL-USE2.5-6 | E2,5-6 | C2 | POLARIZED CAPACITOR, American symbol
1 | 47uF | CPOL-USE2-4 | E2-4 | C7 | POLARIZED CAPACITOR, American symbol
1 | ARDUINO-NANO-3.0 | ARDUINO-NANO-3.0 | ARDUINO-NANO-3.0 | M1 | Arduino Nano 3.0 and compatible devices
2 | DC_MOTOR | DC_MOTOR | DC_MOTOR | U$1, U$2
1 | GY-521MPU6050 | GY-521MPU6050 | GY-521 | U1
1 | HC-05 | HC-05 | HC-05 | U$9
4 | IR_DISTANCE_1X2 | IR_DISTANCE_1X2 | IR_DISTANCE_1X2 | U$3, U$6, U$7, U$8
1 | JST_POWER | JST_POWER | JST_POWER | U$12
2 | K3-1260D | K3-1260D | K3-1260D | U$4, U$10
1 | L293D | L293D | DIL16 | IC1 | PUSH-PULL 4 CHANNEL DRIVER
8 | TPPAD1-13 | TPPAD1-13 | P1-13 | TP1, TP2, TP3, TP4, TP5, TP6, TP7, TP8 | Test pad
1 | XT30-M | XT30-M | XT30-M | U$5

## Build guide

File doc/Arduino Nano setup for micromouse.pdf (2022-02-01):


# Arduino Nano setup for micromouse

### Objective:

### Setup

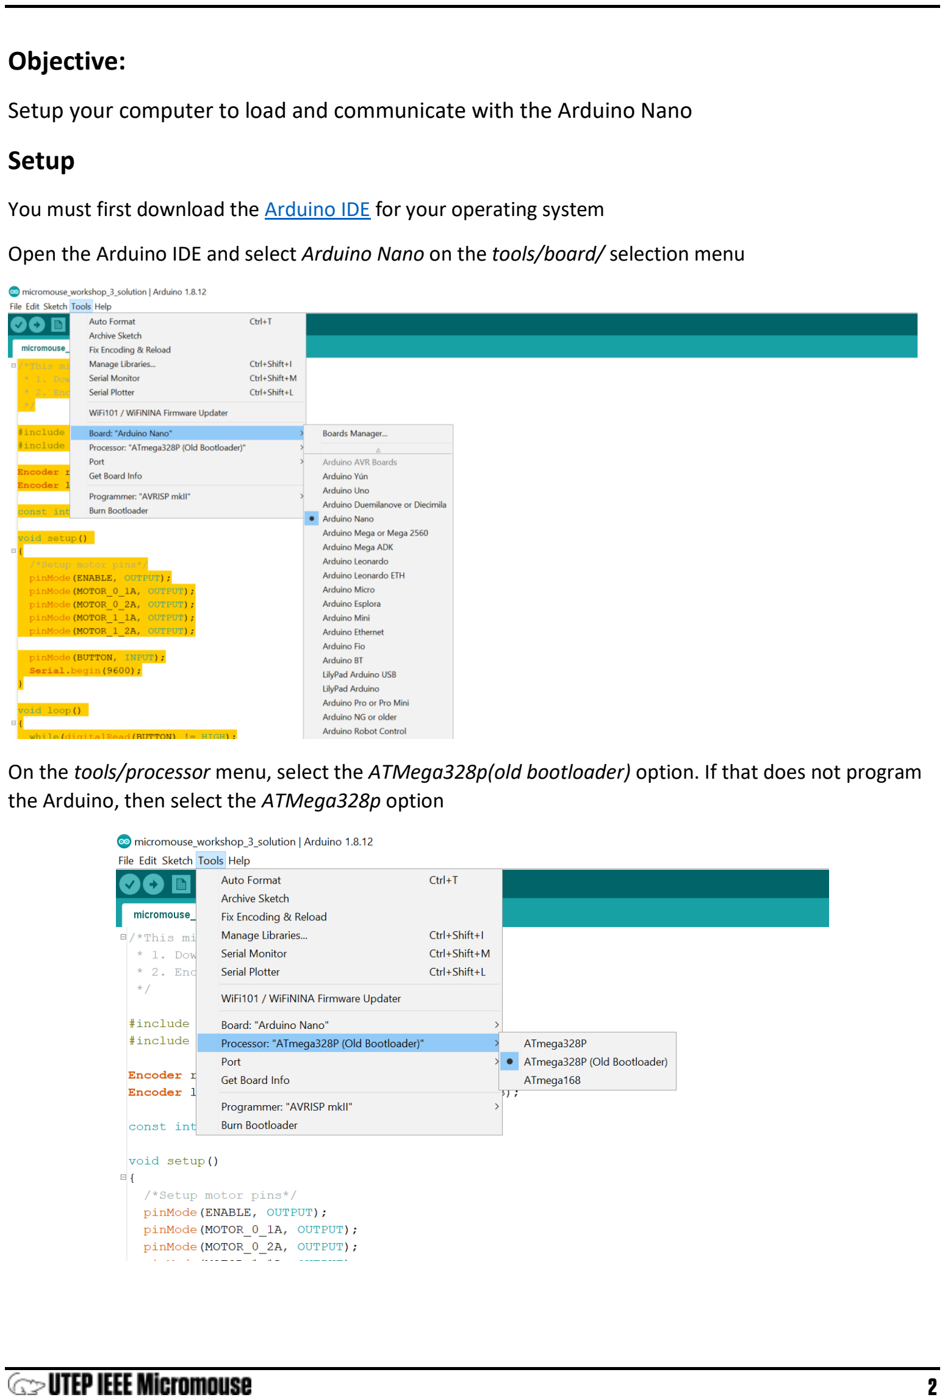
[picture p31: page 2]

2

Setup your computer to load and communicate with the Arduino Nano

You must first download the Arduino IDE (https://www.arduino.cc/en/software) for your operating system

Open the Arduino IDE and select Arduino Nano on the tools/board/ selection menu

On the tools/processor menu, select the ATMega328p(old bootloader) option. If that does not program the Arduino, then select the ATMega328p option

3

Download the drivers for the Arduino Nano by following this link. (https://sparks.gogo.co.nz/ch340.html) Select the appropriate OS for your computer.

Once the download is finished extract the .exe file and run it. Click on install and wait for the installation to finish. Once is finished, restart your computer.

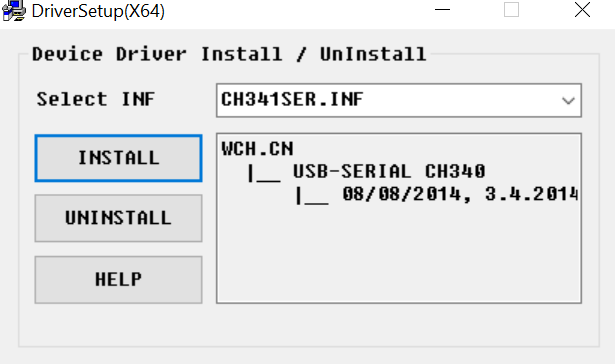
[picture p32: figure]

On the Arduino IDE, you can now see the COM port to communicate with the Arduino Nano

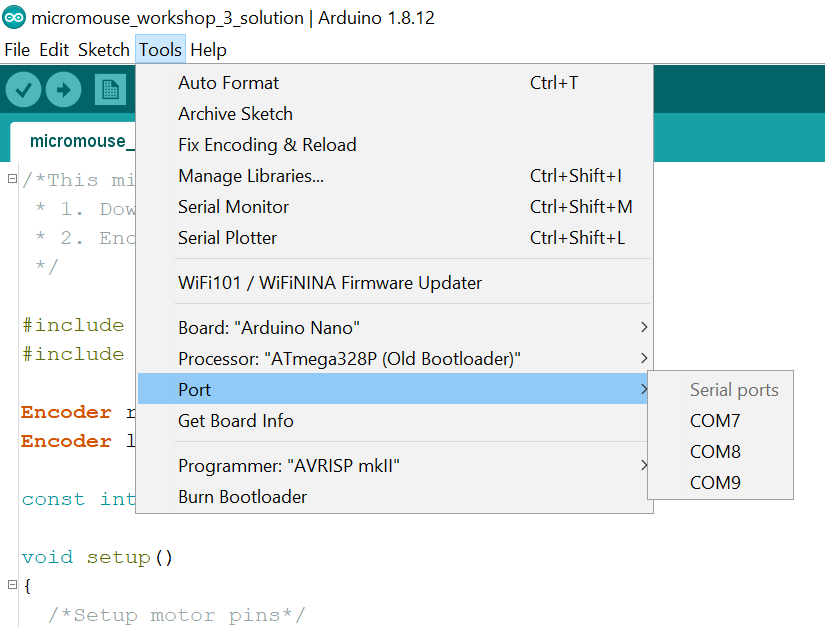
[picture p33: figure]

Try all the ports until one of them successfully programs the Arduino. This will be the same COM port you will use to talk to the Arduino Nano over the serial monitor.

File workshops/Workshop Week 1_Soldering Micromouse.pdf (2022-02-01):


# Workshop Week 1: Soldering your micromouse kit

2

Objective:

Solder the micromouse kit with your teammates. No experience required to solder the micromouse, do not be afraid to ask for assistance.
Background Information:

Today you will be soldering your micromouse with your teammates. All the components along with a soldering station will be provided to your team. The soldering workshop is the first step towards getting to know the components and skills required to assemble a micromouse. Within this document, you will find images of intermediate soldering steps as well as schematics of the entire micromouse board. No written instructions will be given inside of this document, so you must carefully read the schematics and look at the images to properly solder the micromouse board. You can solder the micromouse in any order you like, but we encourage to solder the components as they appear in this document. If you have any questions, please do not hesitate to ask any officer at the workshop.

Some stuff to watch out for:

1. LED, capacitor, and diode polarity. Long lead is positive, short is negative. Only round capacitors have polarity.
2. Resistors will be bent according to the pictures
3. Pay special attention to the assembly of the Infrared (IR) sensors. They come in a separate pair of LEDs and have polarity. You should have an emitter and a receiver; you can identify them by their color. The emitter will have a lighter shade of blue than the emitter.
4. Be patient with the mechanical assembly. Wait for the tools to become available if someone else is using them. Ask for help if you don’t know how to assemble the motors, battery, or caster wheel.
5. Be careful with the orientation of the motor connector. You should see the connector cover the markings where the connector goes. If you can partially see the markings, you have the wrong orientation.

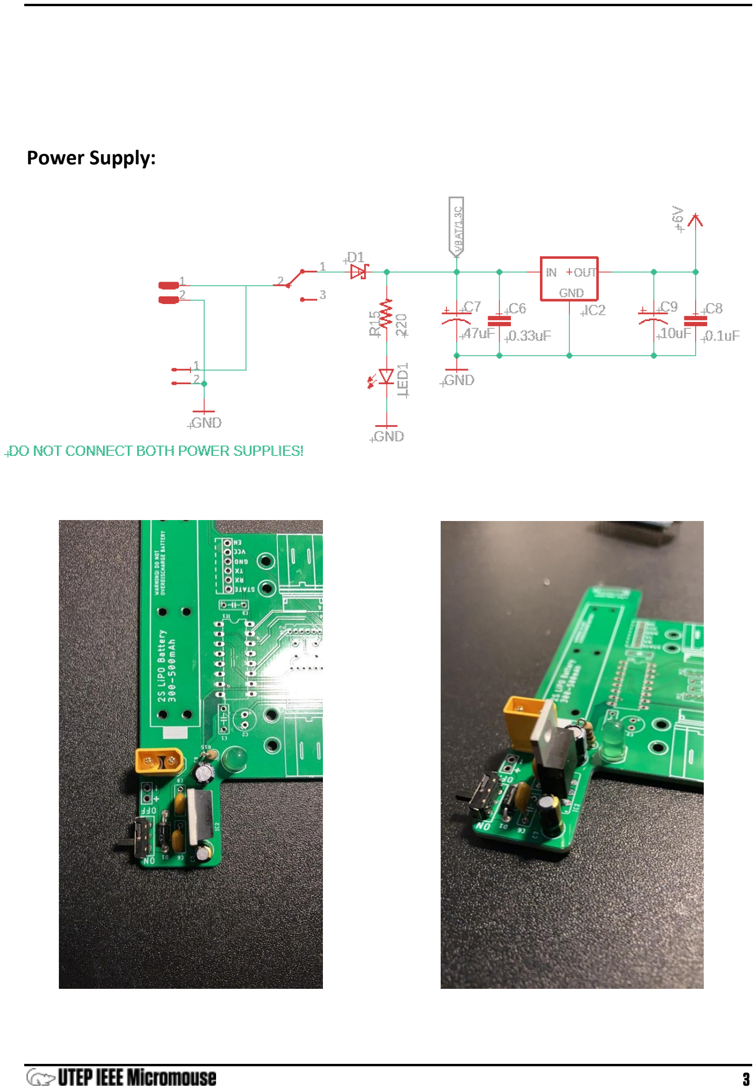
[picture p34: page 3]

3

Power Supply:

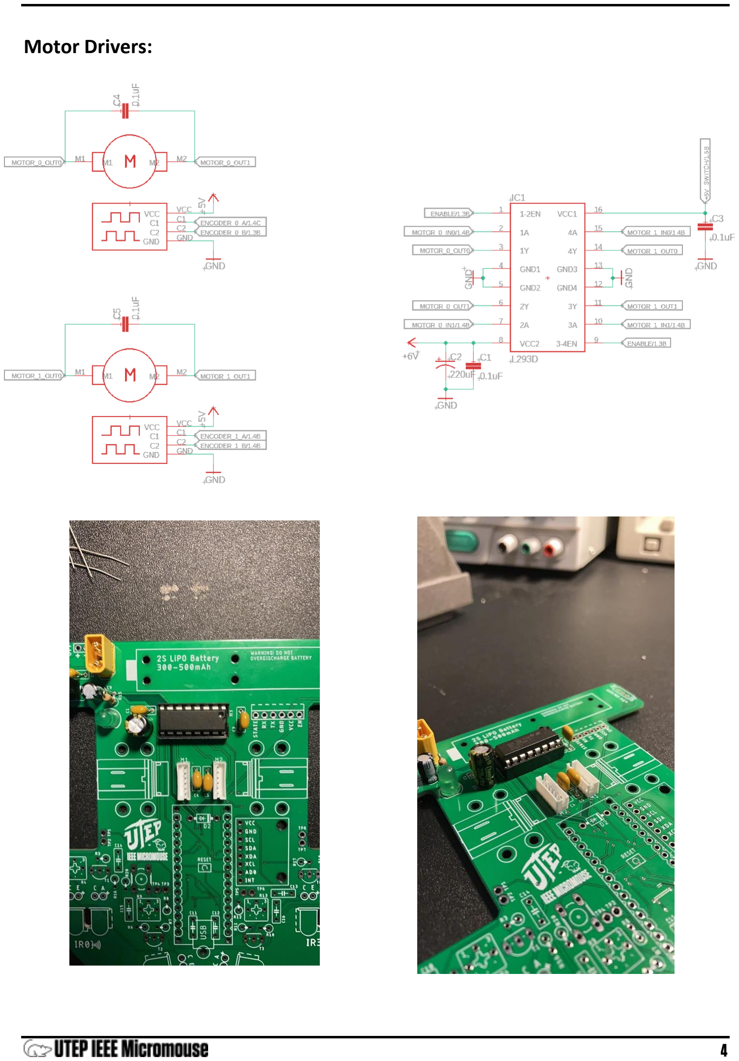
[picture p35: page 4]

4

Motor Drivers:

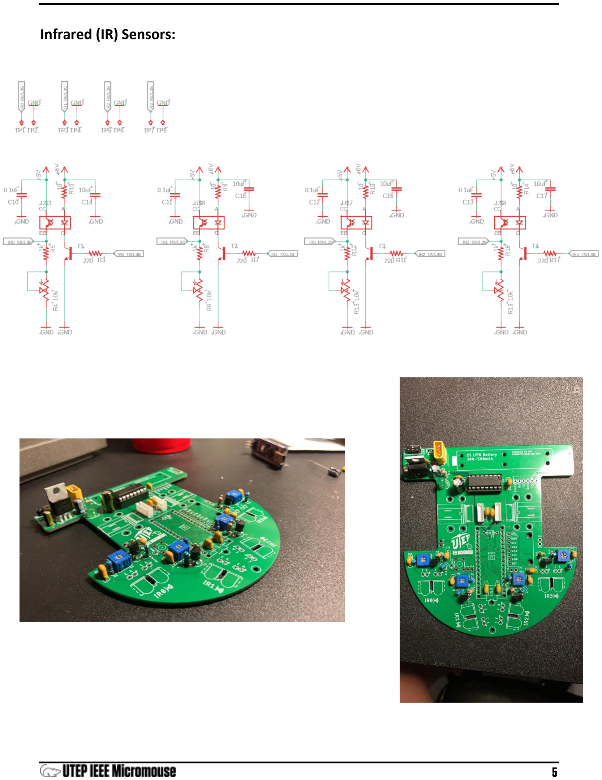
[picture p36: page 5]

5

Infrared (IR) Sensors:

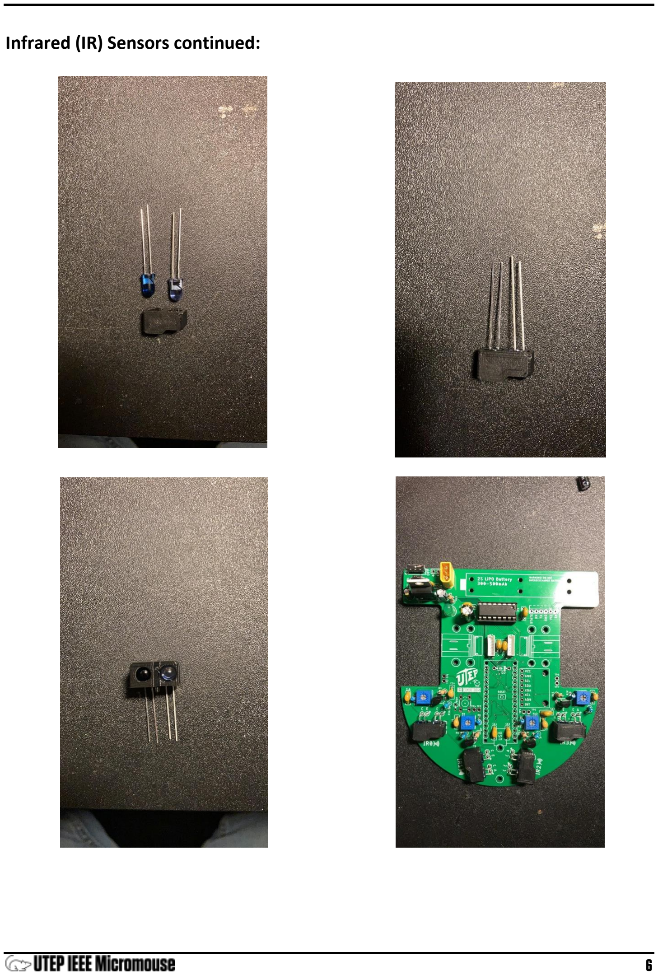
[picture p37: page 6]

6

Infrared (IR) Sensors continued:

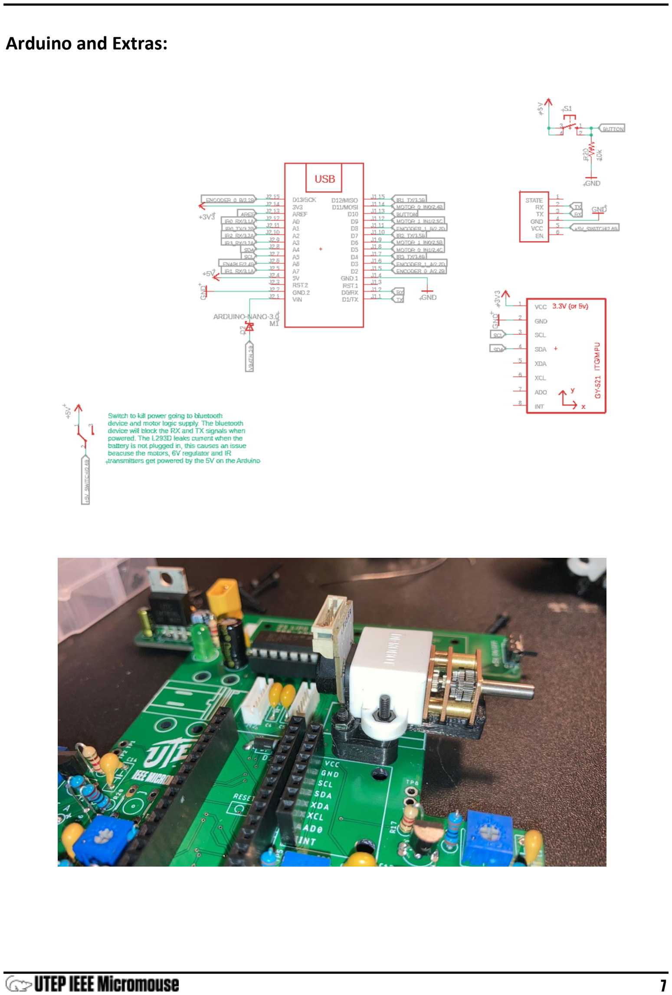
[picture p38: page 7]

7

Arduino and Extras:

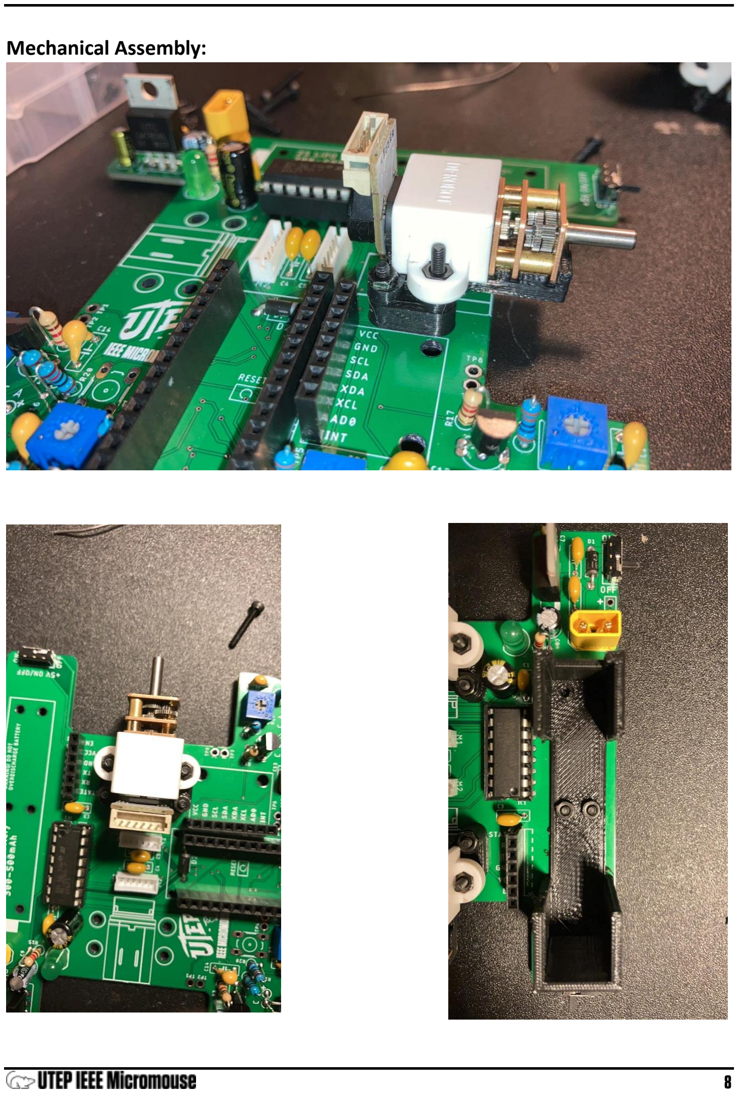
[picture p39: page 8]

8

Mechanical Assembly:

9

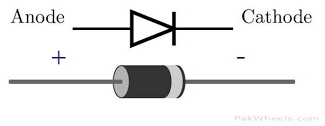
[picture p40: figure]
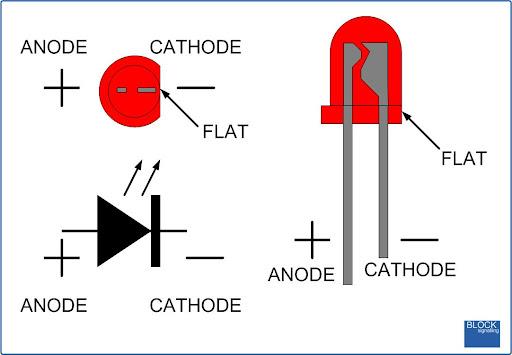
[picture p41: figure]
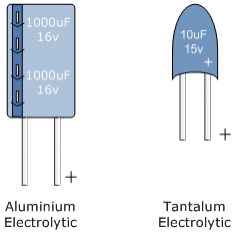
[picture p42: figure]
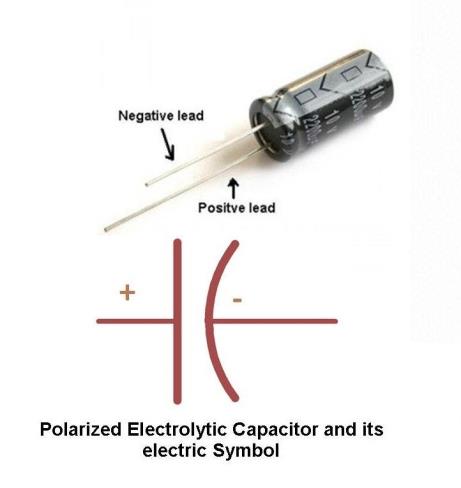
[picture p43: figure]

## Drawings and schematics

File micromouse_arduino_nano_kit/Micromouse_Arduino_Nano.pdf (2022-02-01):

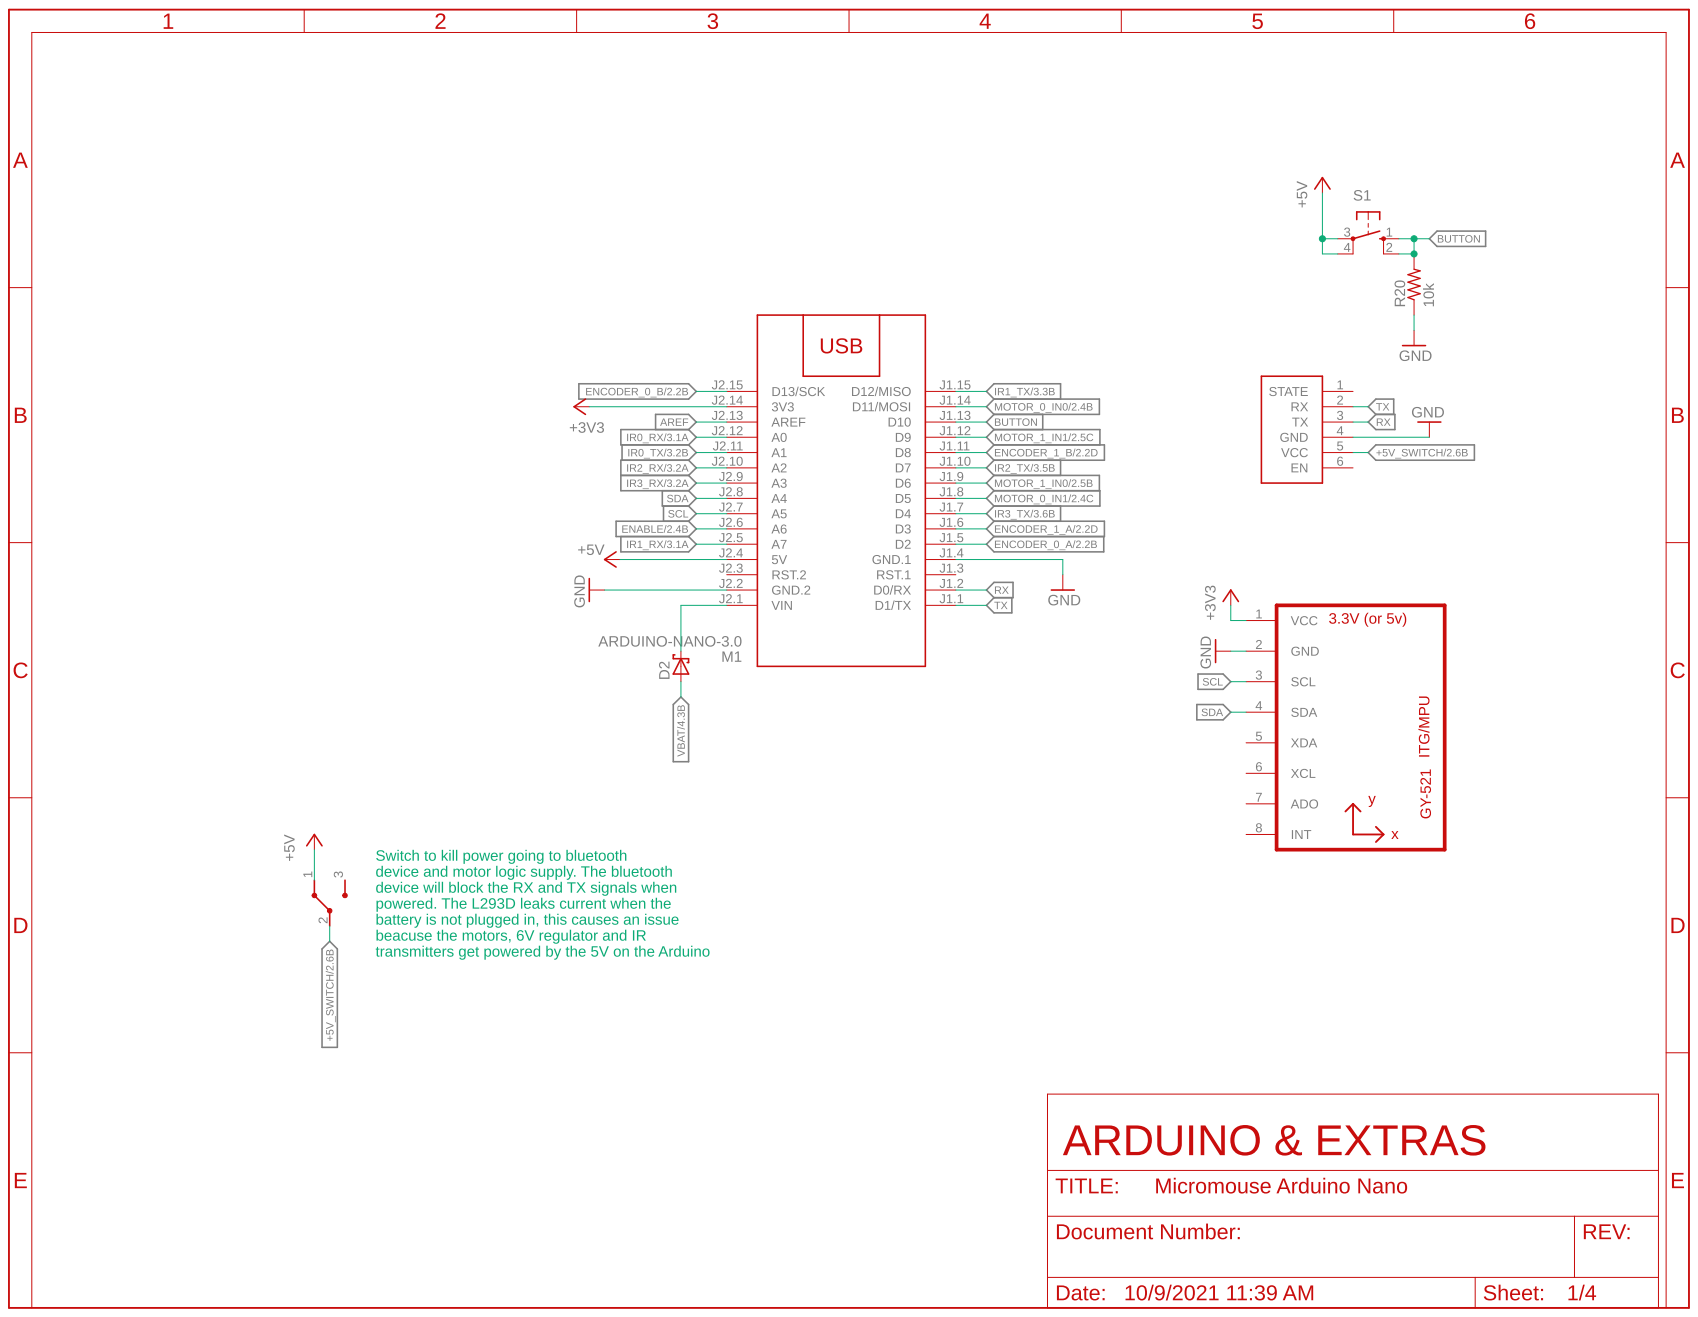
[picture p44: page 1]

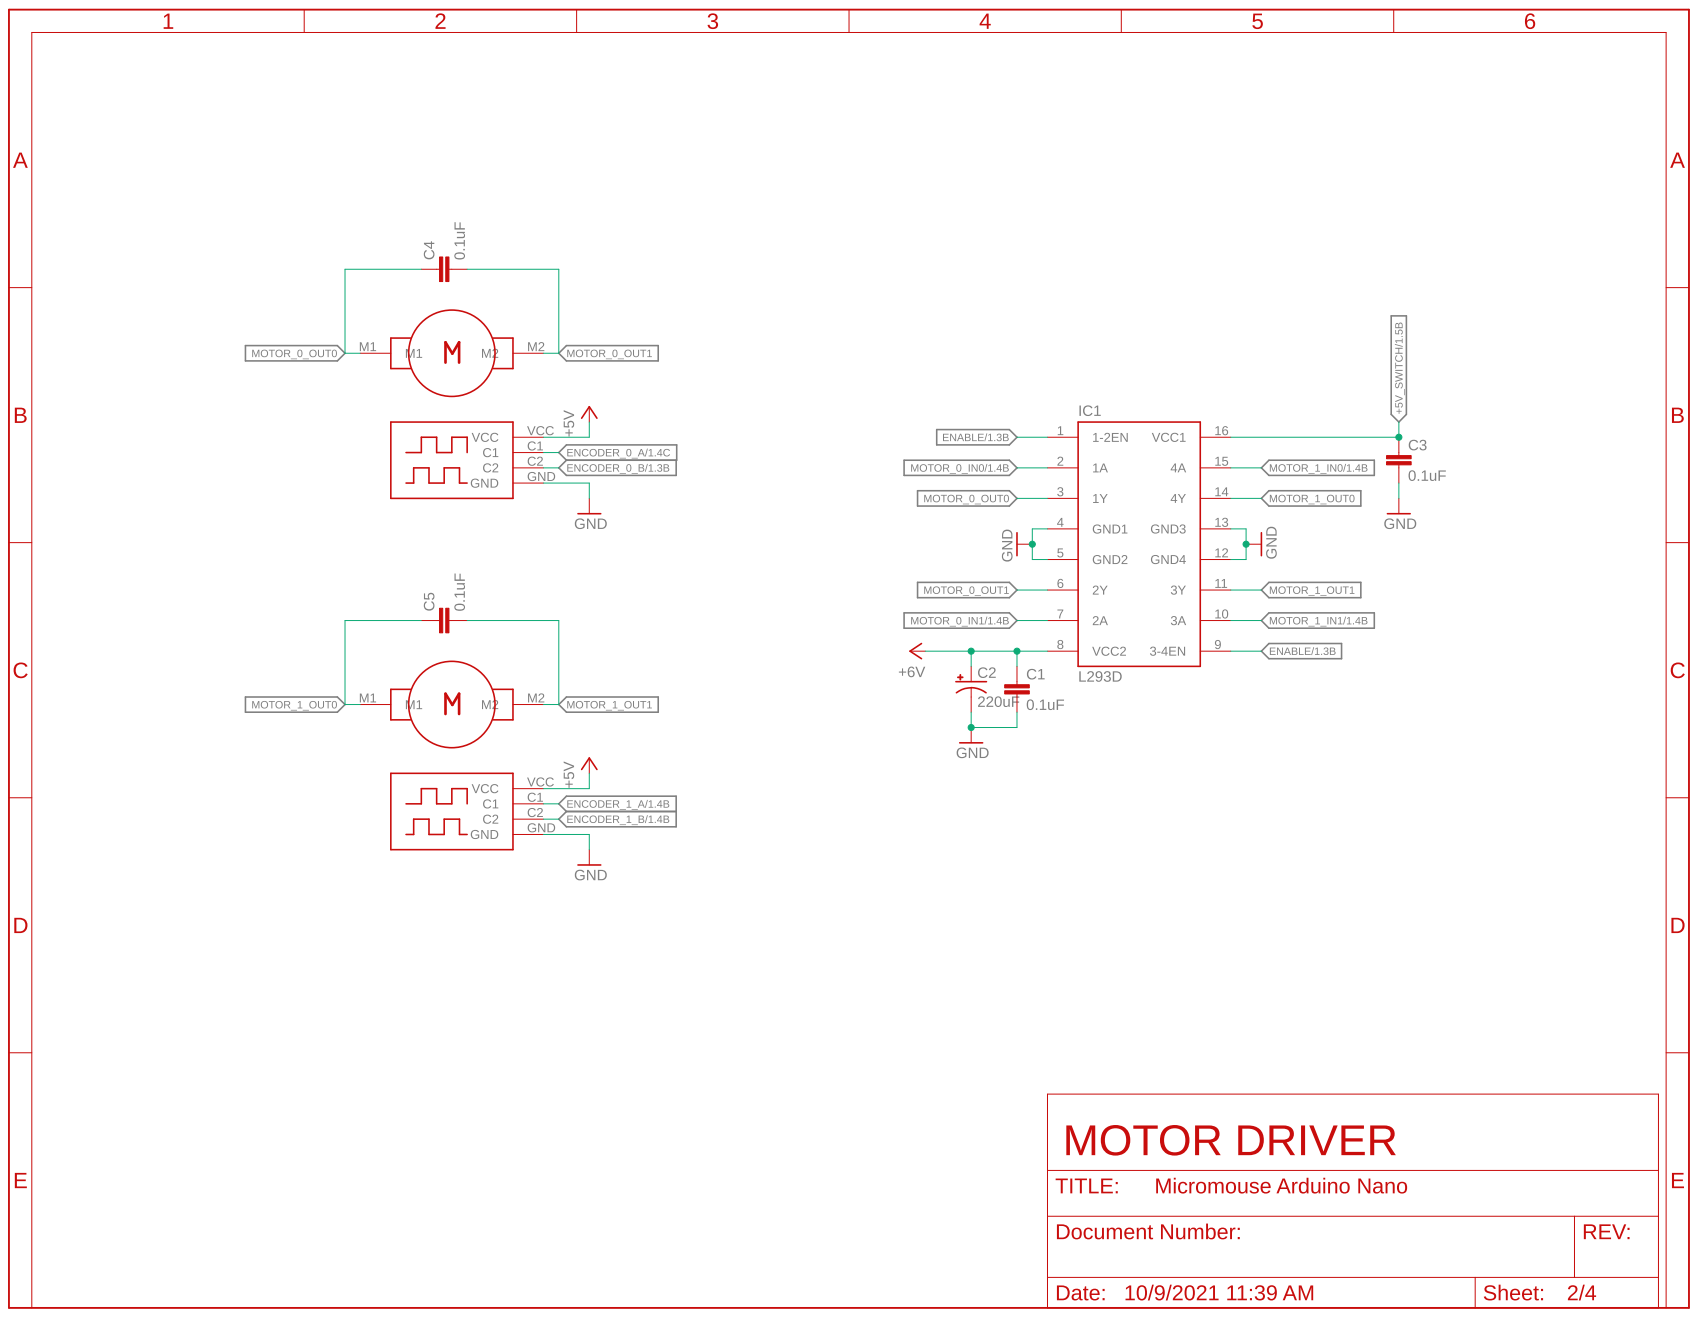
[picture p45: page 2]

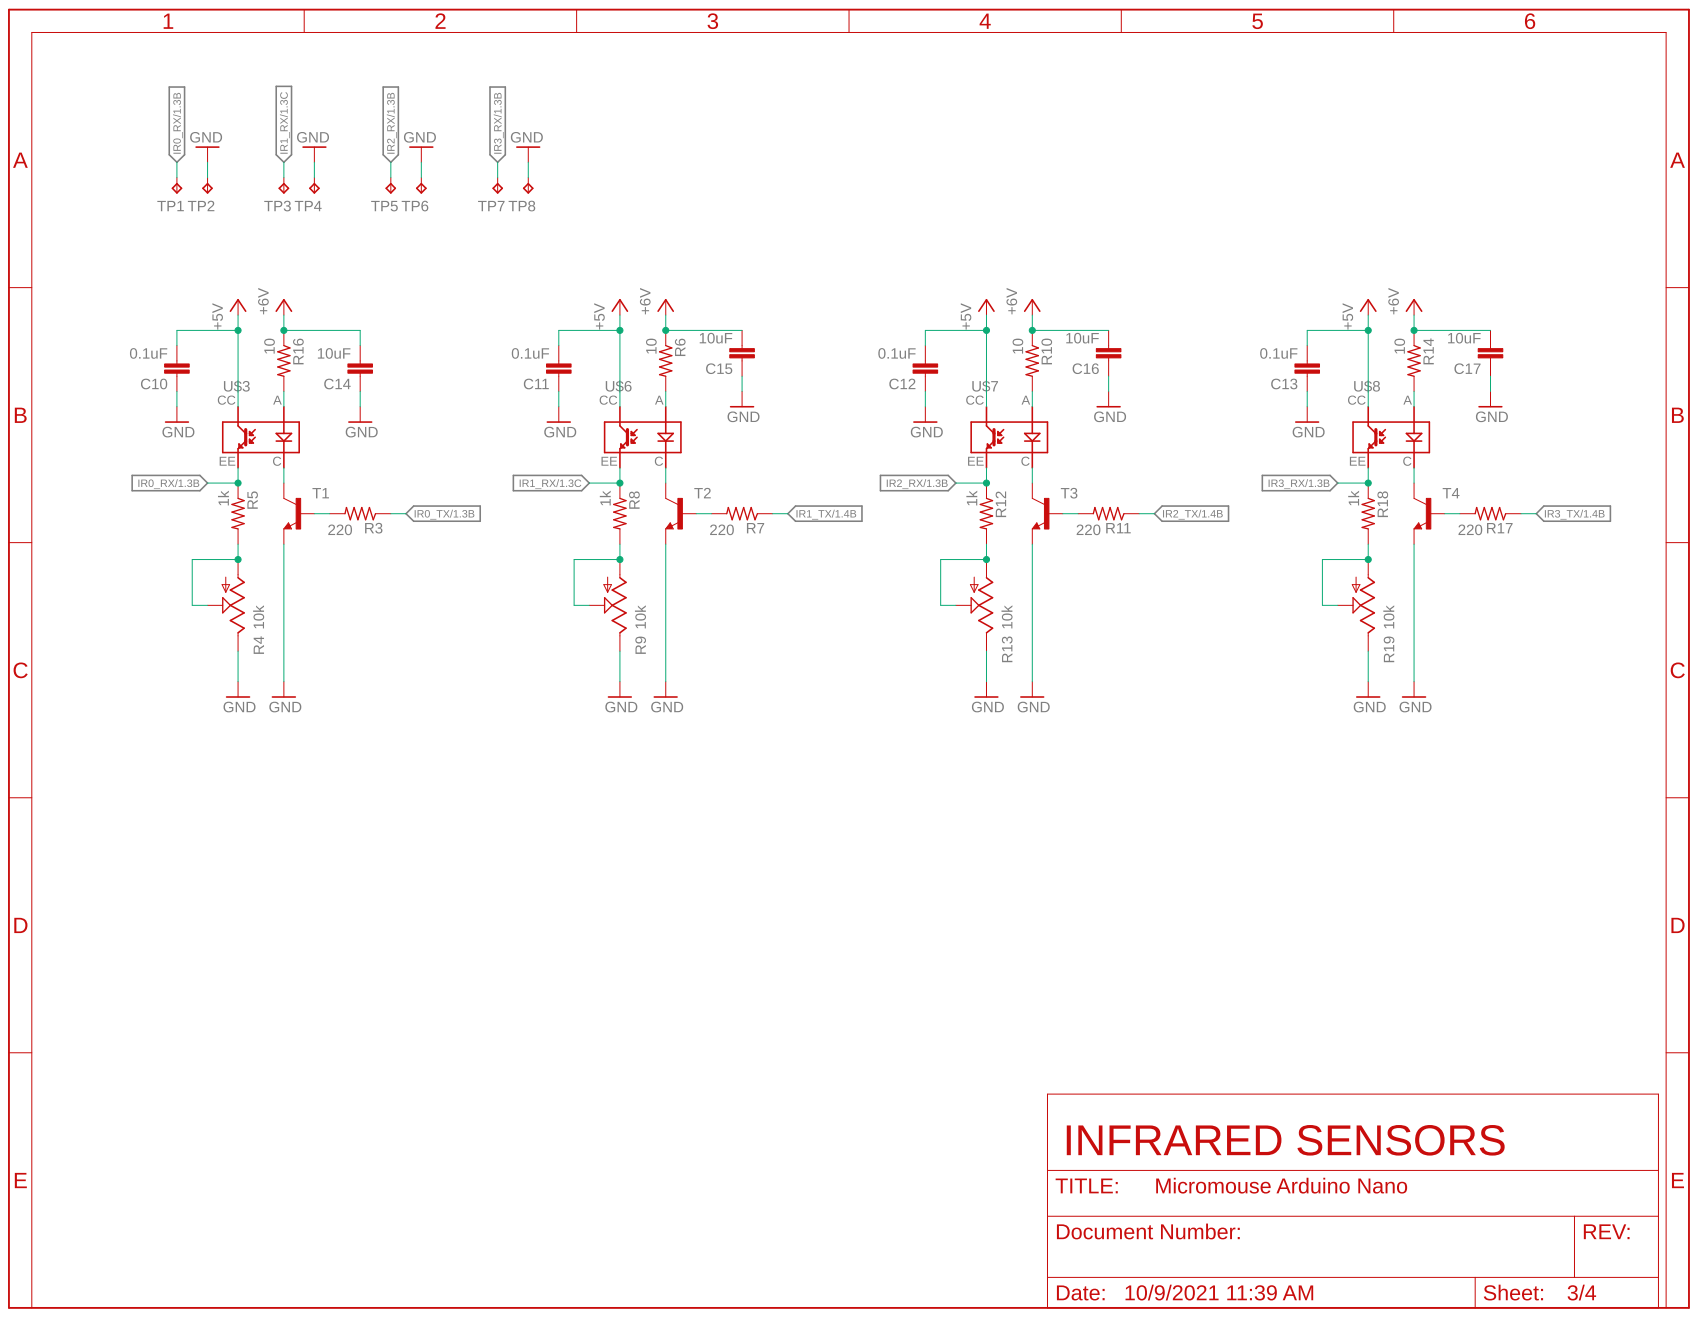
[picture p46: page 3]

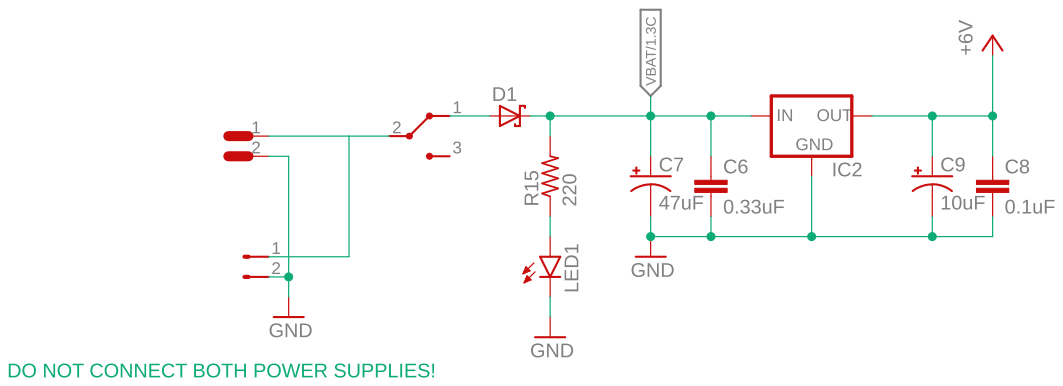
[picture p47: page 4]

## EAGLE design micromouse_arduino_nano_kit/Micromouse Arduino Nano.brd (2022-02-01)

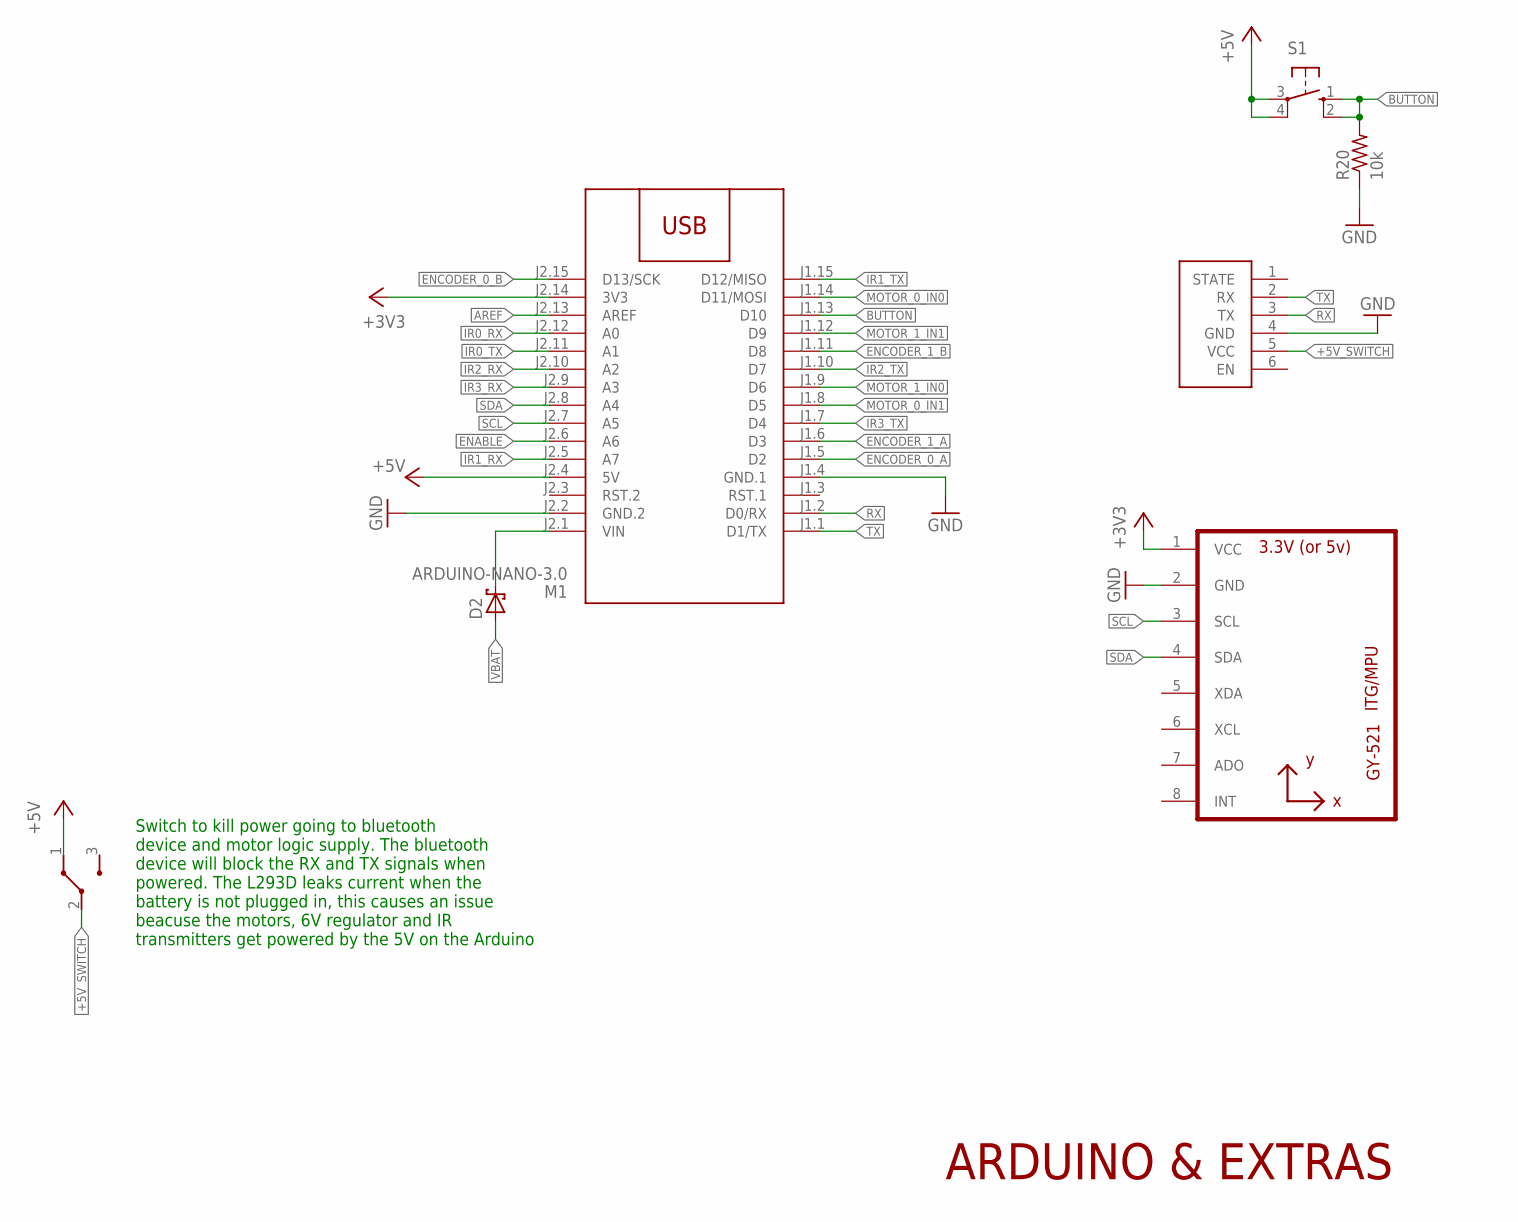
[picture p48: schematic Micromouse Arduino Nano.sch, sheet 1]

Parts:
D2: SCHOTTKY-DIODEDO41-7; DO41-7
M1: ARDUINO-NANO-3.0
R20: 10k; 0207/2V
S1: 10-XX; B3F-10XX
U1: GY-521MPU6050; GY-521
U$9: HC-05
U$10: K3-1260D

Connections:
+3V3: M1.J2.14 (3V3), U1.1 (VCC)
+5V: M1.J2.4 (5V), S1.3, S1.4 (P1), U$10.1; also elsewhere on the board
+5V_SWITCH: U$9.5 (VCC), U$10.2; also elsewhere on the board
AREF: M1.J2.13 (AREF)
BUTTON: M1.J1.13 (D10), R20.2, S1.1 (S), S1.2 (S1)
ENABLE: M1.J2.6 (A6); also elsewhere on the board
ENCODER_0_A: M1.J1.5 (D2); also elsewhere on the board
ENCODER_0_B: M1.J2.15 (D13/SCK); also elsewhere on the board
ENCODER_1_A: M1.J1.6 (D3); also elsewhere on the board
ENCODER_1_B: M1.J1.11 (D8); also elsewhere on the board
GND: M1.J1.4 (GND.1), M1.J2.2 (GND.2), R20.1, U1.2 (GND), U$9.4 (GND); also elsewhere on the board
IR0_RX: M1.J2.12 (A0); also elsewhere on the board
IR0_TX: M1.J2.11 (A1); also elsewhere on the board
IR1_RX: M1.J2.5 (A7); also elsewhere on the board
IR1_TX: M1.J1.15 (D12/MISO); also elsewhere on the board
IR2_RX: M1.J2.10 (A2); also elsewhere on the board
IR2_TX: M1.J1.10 (D7); also elsewhere on the board
IR3_RX: M1.J2.9 (A3); also elsewhere on the board
IR3_TX: M1.J1.7 (D4); also elsewhere on the board
MOTOR_0_IN0: M1.J1.14 (D11/MOSI); also elsewhere on the board
MOTOR_0_IN1: M1.J1.8 (D5); also elsewhere on the board
MOTOR_1_IN0: M1.J1.9 (D6); also elsewhere on the board
MOTOR_1_IN1: M1.J1.12 (D9); also elsewhere on the board
unnamed: D2.C, M1.J2.1 (VIN)
RX: M1.J1.2 (D0/RX), U$9.3 (TX)
SCL: M1.J2.7 (A5), U1.3 (SCL)
SDA: M1.J2.8 (A4), U1.4 (SDA)
TX: M1.J1.1 (D1/TX), U$9.2 (RX)
VBAT: D2.A; also elsewhere on the board

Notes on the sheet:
Switch to kill power going to bluetooth device and motor logic supply. The bluetooth device will block the RX and TX signals when powered. The L293D leaks current when the battery is not plugged in, this causes an issue beacuse the motors, 6V regulator and IR transmitters get powered by the 5V on t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
ARDUINO & EXTRAS

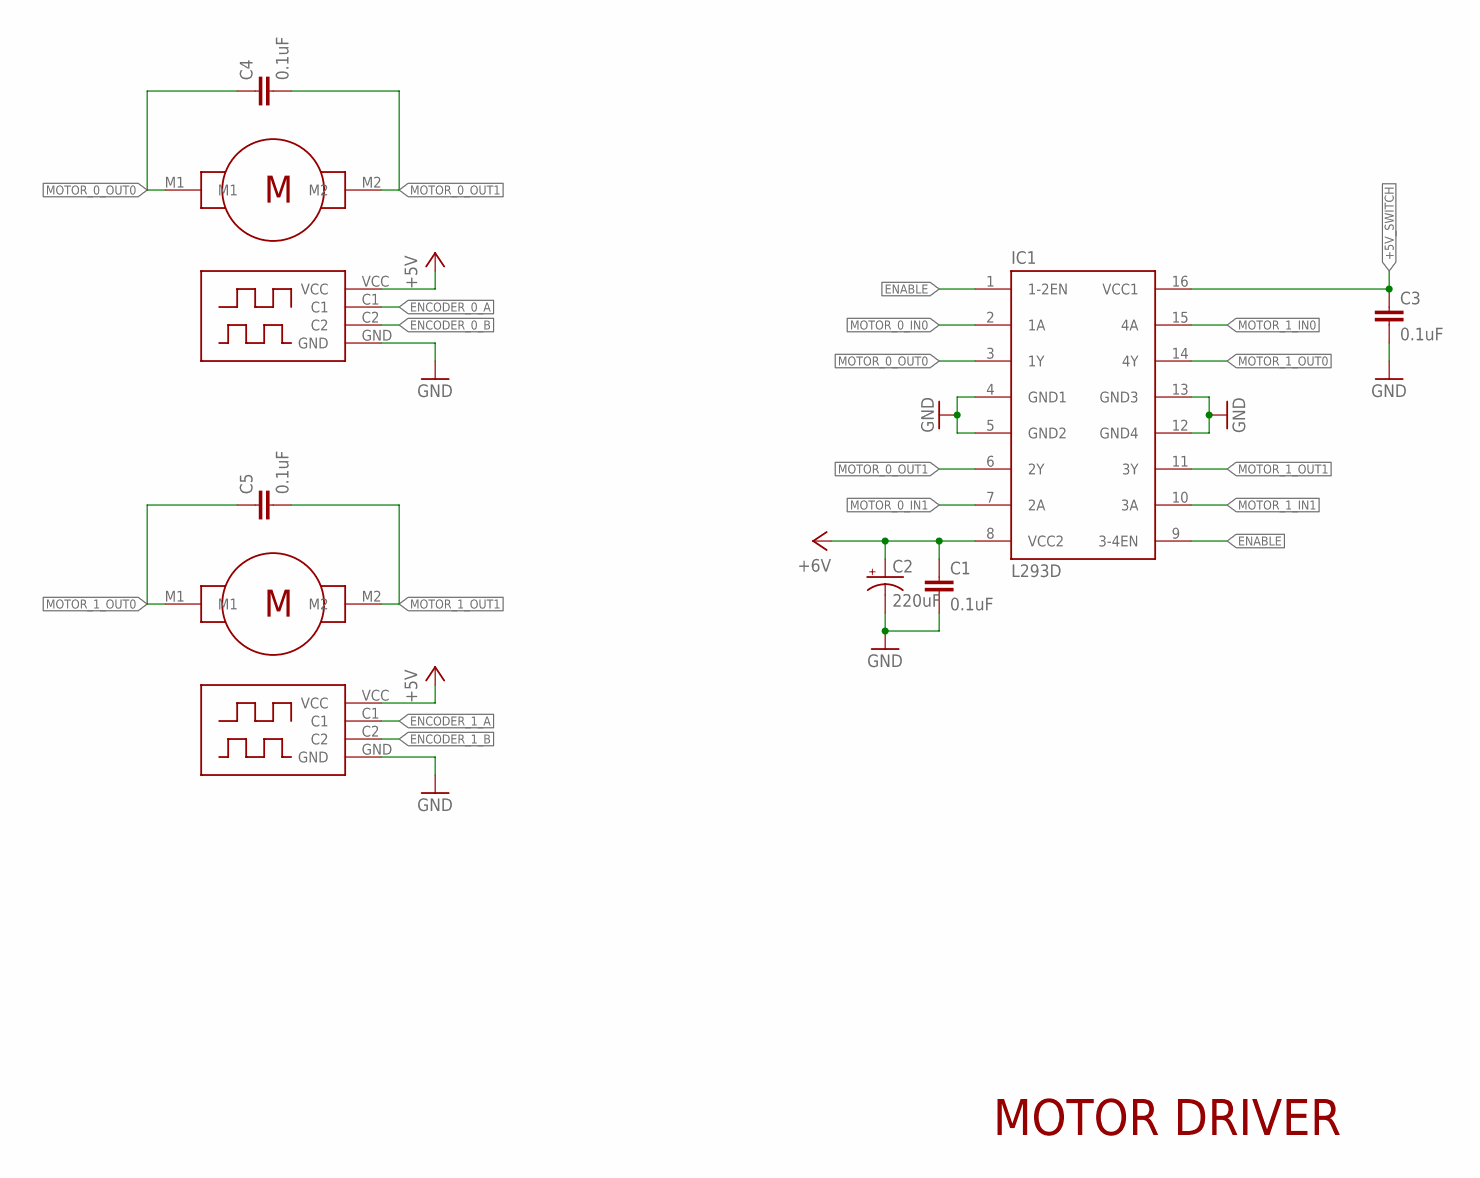
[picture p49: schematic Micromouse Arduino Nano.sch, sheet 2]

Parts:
C1, C3, C4, C5: 0.1uF; C050-025X075
C2: 220uF; E2,5-6
IC1: L293D; DIL16
U$1, U$2: DC_MOTOR

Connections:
+5V: U$1.VCC, U$2.VCC; also elsewhere on the board
+5V_SWITCH: C3.1, IC1.16 (VCC1); also elsewhere on the board
ENABLE: IC1.1 (1-2EN), IC1.9 (3-4EN); also elsewhere on the board
ENCODER_0_A: U$1.C1; also elsewhere on the board
ENCODER_0_B: U$1.C2; also elsewhere on the board
ENCODER_1_A: U$2.C1; also elsewhere on the board
ENCODER_1_B: U$2.C2; also elsewhere on the board
GND: C1.2, C2.-, C3.2, IC1.4 (GND1), IC1.5 (GND2), IC1.12 (GND4), IC1.13 (GND3), U$1.GND, U$2.GND; also elsewhere on the board
MOTOR_0_IN0: IC1.2 (1A); also elsewhere on the board
MOTOR_0_IN1: IC1.7 (2A); also elsewhere on the board
MOTOR_0_OUT0: C4.1, IC1.3 (1Y), U$1.M1
MOTOR_0_OUT1: C4.2, IC1.6 (2Y), U$1.M2
MOTOR_1_IN0: IC1.15 (4A); also elsewhere on the board
MOTOR_1_IN1: IC1.10 (3A); also elsewhere on the board
MOTOR_1_OUT0: C5.1, IC1.14 (4Y), U$2.M1
MOTOR_1_OUT1: C5.2, IC1.11 (3Y), U$2.M2
VCC: C1.1, C2.+, IC1.8 (VCC2); also elsewhere on the board

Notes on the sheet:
MOTOR DRIVER

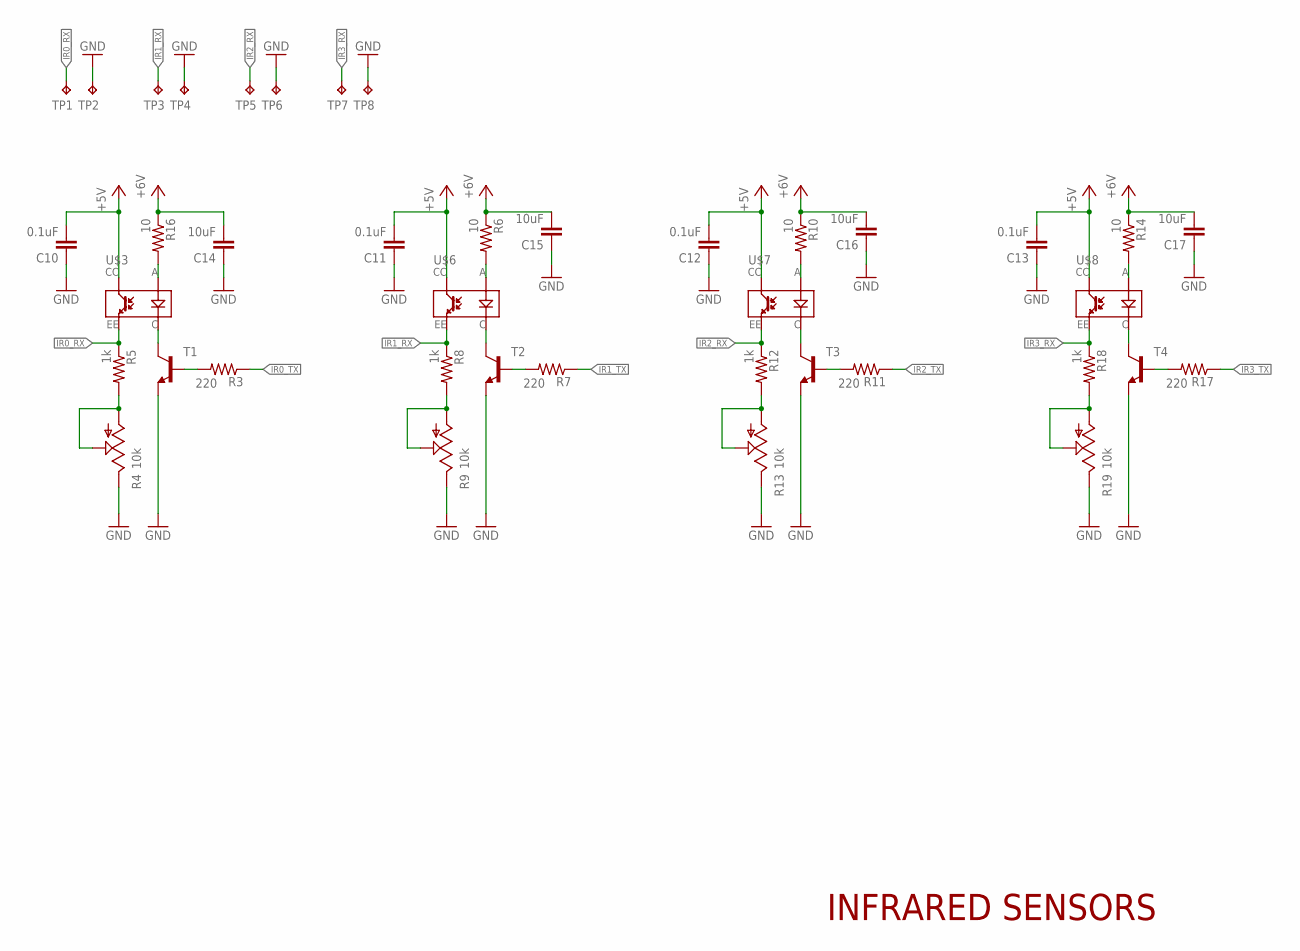
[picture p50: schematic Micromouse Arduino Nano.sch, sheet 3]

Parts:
C10, C11, C12, C13: 0.1uF; C050-025X075
C14, C15, C16, C17: 10uF; C050-025X075
R3, R7, R11, R17: 220; 0207/2V
R4, R9, R13, R19: 10k; CT6
R5, R8, R12, R18: 1k; 0207/2V
R6, R10, R14, R16: 10; 0207/2V
T1, T2, T3, T4: 2N4124-NPN-TO92-CBE; TO92-CBE
TP1, TP2, TP3, TP4, TP5, TP6, TP7, TP8: TPPAD1-13; P1-13
U$3, U$6, U$7, U$8: IR_DISTANCE_1X2

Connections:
+5V: C10.2, C11.2, C12.2, C13.2, U$3.CC, U$6.CC, U$7.CC, U$8.CC; also elsewhere on the board
GND: C10.1, C11.1, C12.1, C13.1, C14.1, C15.1, C16.1, C17.1, R4.E, R9.E, R13.E, R19.E, T1.E, T2.E, T3.E, T4.E, TP2.TP, TP4.TP, TP6.TP, TP8.TP; also elsewhere on the board
IR0_RX: R5.1, TP1.TP, U$3.EE; also elsewhere on the board
IR0_TX: R3.1; also elsewhere on the board
IR1_RX: R8.1, TP3.TP, U$6.EE; also elsewhere on the board
IR1_TX: R7.1; also elsewhere on the board
IR2_RX: R12.1, TP5.TP, U$7.EE; also elsewhere on the board
IR2_TX: R11.1; also elsewhere on the board
IR3_RX: R18.1, TP7.TP, U$8.EE; also elsewhere on the board
IR3_TX: R17.1; also elsewhere on the board
unnamed: T1.C, U$3.C
unnamed: R3.2, T1.B
unnamed: R16.2, U$3.A
unnamed: R6.2, U$6.A
unnamed: R4.A, R4.S, R5.2
unnamed: T2.C, U$6.C
unnamed: R7.2, T2.B
unnamed: R8.2, R9.A, R9.S
unnamed: R10.2, U$7.A
unnamed: T3.C, U$7.C
unnamed: R11.2, T3.B
unnamed: R12.2, R13.A, R13.S
unnamed: R14.2, U$8.A
unnamed: T4.C, U$8.C
unnamed: R17.2, T4.B
unnamed: R18.2, R19.A, R19.S
VCC: C14.2, C15.2, C16.2, C17.2, R6.1, R10.1, R14.1, R16.1; also elsewhere on the board

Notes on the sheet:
INFRARED SENSORS

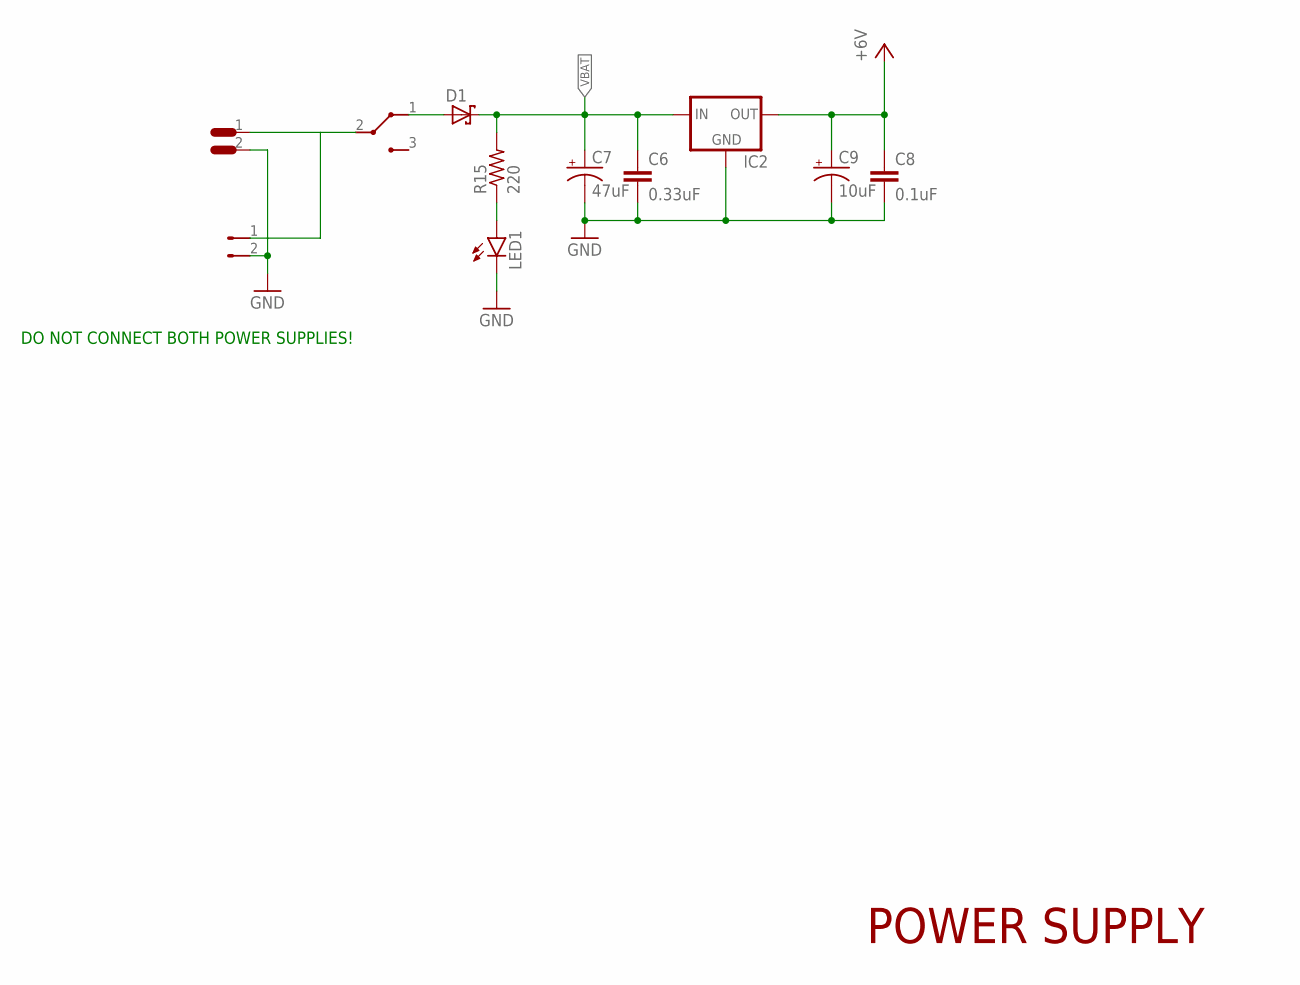
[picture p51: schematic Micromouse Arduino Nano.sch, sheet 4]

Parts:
C6: 0.33uF; C050-025X075
C7: 47uF; E2-4
C8: 0.1uF; C050-025X075
C9: 10uF; E2,5-5
D1: SCHOTTKY-DIODEDO41-7; DO41-7
IC2: 78XXS
LED1: LED5MM
R15: 220; 0207/2V
U$4: K3-1260D
U$5: XT30-M
U$12: JST_POWER

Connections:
GND: C6.2, C7.-, C8.2, C9.-, IC2.GND, LED1.K (C), U$5.2, U$12.2; also elsewhere on the board
unnamed: D1.A, U$4.1
unnamed: U$4.2, U$5.1, U$12.1
unnamed: LED1.A, R15.1
VBAT: C6.1, C7.+, D1.C, IC2.IN, R15.2; also elsewhere on the board
VCC: C8.1, C9.+, IC2.OUT; also elsewhere on the board

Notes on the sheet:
DO NOT CONNECT BOTH POWER SUPPLIES!
POWER SUPPLY

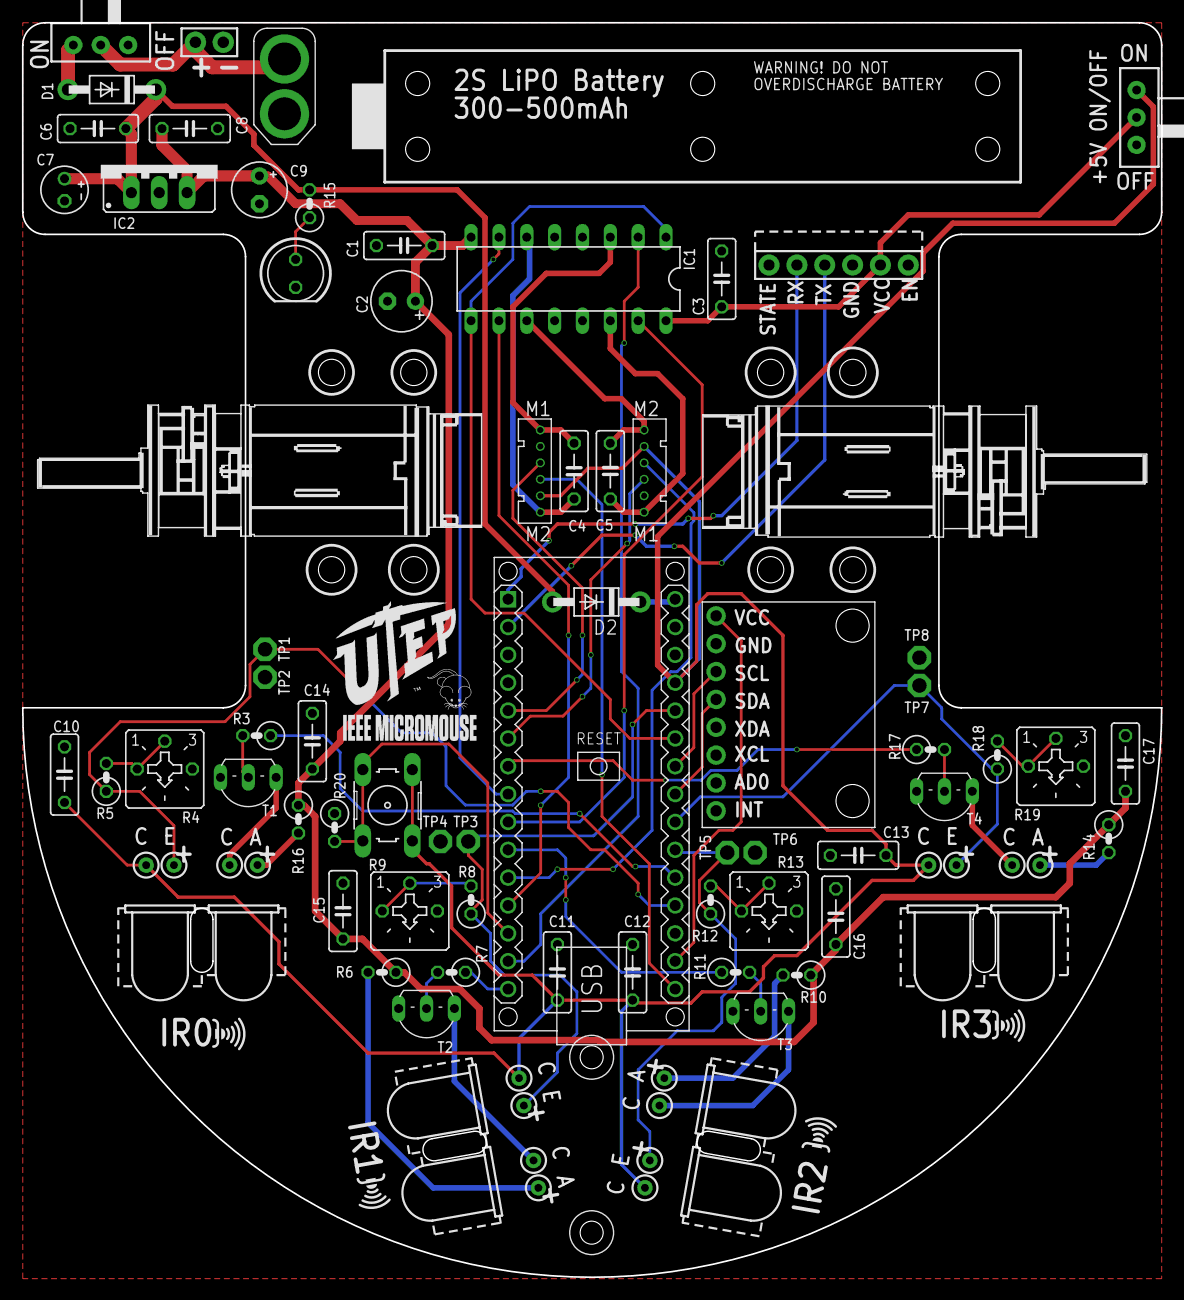
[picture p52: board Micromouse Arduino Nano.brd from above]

Board: 2 copper layers, 103.9 x 114.4 mm, 76 parts (0 on the bottom side), 52 nets.

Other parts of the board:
U$11: CASTER_WHEEL
U$13: MICROMOUSE
U$14, U$15, U$16, U$17: IR_SENSOR
U$18: MICROMOUSE_TEXT
U$19: MINER_LOGO
U$20: MICROMOUSE_TEXT_1
U$21: LIPO

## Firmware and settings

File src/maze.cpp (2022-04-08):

#include "maze.h"
#include "stack.h"

/*Virtual mouse object*/
mouse_t mouse = {.x = 0, .y = 0, .heading = NORTH};

/*Maze cells array*/
cell_t maze[MAZE_WIDTH][MAZE_HEIGHT];

/*TODO: We should be able to bitwise OR walls, right now this 
 * function does not support it. Think of a way to do it!
 */
int8_t maze_set_wall(uint8_t x, uint8_t y, uint8_t wall)
{
  if(CHECK_BOUNDARIES(x, y)) return -1;
  
  maze[x][y].walls |= wall;

  switch(wall)
  {
    case NORTH:
      maze[x][y-1].walls |= SOUTH;
      break;
    case EAST:
      maze[x+1][y].walls |= WEST;
      break;
    case SOUTH: 
      maze[x][y+1].walls |= NORTH;
      break;
    case WEST:
      maze[x-1][y].walls |= EAST;
      break; 
  }
}

int8_t maze_get_walls(uint8_t x, uint8_t y)
{
  if(CHECK_BOUNDARIES(x, y)) return -1;
   
  return maze[x][y].walls;
}

int8_t maze_set_value(uint8_t x, uint8_t y, uint8_t value)
{
  if(CHECK_BOUNDARIES(x, y)) return -1;
  
  maze[x][y].value = value;
}

int8_t maze_get_value(uint8_t x, uint8_t y)
{
  if(CHECK_BOUNDARIES(x, y)) return -1;

   return maze[x][y].value;
}

cell_t *maze_get_cell(uint8_t x, uint8_t y)
{
  return &maze[x][y];
}

void maze_init(uint8_t target_x, uint8_t target_y)
{
  if(CHECK_BOUNDARIES(target_x, target_y)) return;
  
  for(uint8_t y = 0; y < MAZE_HEIGHT; y++)
  {
    for(uint8_t x = 0; x < MAZE_WIDTH; x++)
    {
      maze[x][y].value = abs(target_x - x) + abs(target_y - y);
      maze[x][y].pos = X_POS(x) | Y_POS(y);  

      if(x == 0)                 maze[x][y].walls |= WEST;
      if(x == (MAZE_WIDTH - 1))  maze[x][y].walls |= EAST;
      if(y == 0)                 maze[x][y].walls |= NORTH;
      if(y == (MAZE_HEIGHT - 1)) maze[x][y].walls |= SOUTH;
    }
  }
}

/*Print routine for VT100 terminals. Recommended terminal is putty*/
void maze_print(void)
{
  /*Clear previous maze*/
  Serial.print("\x1B[2J");
  
  for(uint8_t y = 0; y < MAZE_HEIGHT; y++)
  {
    for(uint8_t x = 0; x < MAZE_WIDTH; x++)
    {
      uint8_t cy = 4*x + 1;
      uint8_t cx = 2*y + 1;

      /*Print cell value*/
      Serial.print("\x1B[");
      Serial.print(cx+1);
      Serial.print(";");
      Serial.print(cy+2);
      Serial.print("H");
      Serial.print(maze[x][y].value, DEC);

      /*Print north wall if present*/
      if(maze[x][y].walls & NORTH)
      {
        Serial.print("\x1B[");
        Serial.print(cx);
        Serial.print(";");
        Serial.print(cy);
        Serial.print("H");
        Serial.print("+---+");
      }
      
      /*Print east wall if present*/
      if(maze[x][y].walls & EAST)
      {
        Serial.print("\x1B[");
        Serial.print(cx+1);
        Serial.print(";");
        Serial.print(cy+4);
        Serial.print("H");
        Serial.print("|");
      }

      /*Print south wall if present*/
      if(maze[x][y].walls & SOUTH)
      {
        Serial.print("\x1B[");
        Serial.print(cx+2);
        Serial.print(";");
        Serial.print(cy);
        Serial.print("H");
        Serial.print("+---+");
      }

      /*Print west wall if present*/
      if(maze[x][y].walls & WEST)
      {
        Serial.print("\x1B[");
        Serial.print(cx+1);
        Serial.print(";");
        Serial.print(cy);
        Serial.print("H");
        Serial.print("|");
      }
    }
  }

  /*Print mouse's position and heading*/
  uint8_t mx = 2*mouse.y + 1;
  uint8_t my = 4*mouse.x + 1;

  Serial.print("\x1B[");
  Serial.print(mx+1);
  Serial.print(";");
  Serial.print(my+2);
  Serial.print("H");

  switch(mouse.heading)
  {
    case NORTH:
      Serial.print("^");
      break;
    case EAST:
      Serial.print(">");
      break;
    case SOUTH:
      Serial.print("V");
      break;
    case WEST:
      Serial.print("<");
      break;
  }
}

/*FlOOD FILL CODE GOES HERE***************************************************/
void flood_fill(int x, int y)
{
  /*Neighbor offsets for all orientations*/
  int8_t neighbor_offset[4][2] = 
  {
    {0, -1}, 
    {1,  0},  
    {0,  1},
    {-1, 0},
  };

  /*Pointer to data structure. 
  See https://overiq.com/c-programming-101/pointer-to-a-structure-in-c/ */
  cell_t *current;
  cell_t *neighbor;

  /*Get current cell from maze*/
  current = maze_get_cell(x, y);

  /*Push current cell to the stack*/
  stack_push(current);

  /*Keep running until the stack is not empty*/
  while(!stack_empty())
  {
    /*Pop cell from the stack*/
    stack_pop(current);

    /*If this is the target cell, then do nothing*/
    if(current->value == 0) break;
    
    /*Get position from popped cell*/
    uint8_t cx = GET_X_POS(current->pos);
    uint8_t cy = GET_Y_POS(current->pos);

    /*Find the open neighbor with the lowest value*/
    uint8_t minimum = 255;
    for(int i = 0; i < 4; i++)
    {
      if((current->walls & (1 << i)) == 0)
      {
        /*Get neighborhs x and y coordinates*/
        int8_t nx = cx + neighbor_offset[i][0];
        int8_t ny = cy + neighbor_offset[i][1];

        /*Get neighbor cell pointer from the maze*/
        neighbor = maze_get_cell(nx, ny);
        /*If the neighbor is less than the minimum,
         * then set this cell value as the new minimum*/
        if(neighbor->value < minimum)
        {
          minimum = neighbor->value;
        }
      }
    }

    /*If the curren cell value is not one less 
     * than the minimum ...
     */
    if(minimum != (current->value - 1))
    {
      /*Increment the current cell value by the minimum + 1*/
      current->value = minimum + 1;

      /*Push all neighbors into the stack*/
      for(int i = 0; i < 4; i++)
      {
        /*Get neighborhs x and y coordinates*/
        int8_t nx = cx + neighbor_offset[i][0];
        int8_t ny = cy + neighbor_offset[i][1];

        /*Check that cell is not out of bounds*/
        if((nx > 0)                 && 
           (nx < (MAZE_WIDTH - 1))  &&
           (ny > 0)                 &&
           (ny < (MAZE_HEIGHT - 1)))
        {
            /*Get neighbor cell pointer from the maze*/
            neighbor = maze_get_cell(nx, ny);
            if(neighbor->value != 0)
            {
              /*Push the neighbor into the stack if the value
               * is not equal to 0*/
              stack_push(neighbor);   
            }
        }
      }
    }
  }
}

/*FlOOD FILL ENDS HERE********************************************************/

void mouse_set_x(int8_t x)
{
  if(x > (MAZE_WIDTH - 1)) { x = MAZE_WIDTH - 1; }
  if(x < 0) { x = 0; }
  
  mouse.x = x;
}

void mouse_set_y(int8_t y)
{
  if(y > (MAZE_HEIGHT - 1)) { y = MAZE_HEIGHT - 1; }
  if(y < 0) { y = 0; }
  
  mouse.y = y;
}

int8_t mouse_get_x(void)
{
  return mouse.x;
}

int8_t mouse_get_y(void)
{
  return mouse.y;
}

void mouse_set_heading(uint8_t heading)
{
  mouse.heading = heading;
}

uint8_t mouse_get_heading(void)
{
   return mouse.heading;
}

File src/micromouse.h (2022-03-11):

#ifndef MICROMOUSE_H_
#define MICROMOUSE_H_

#include <Arduino.h>
#include <stdbool.h>

/*Motor definitions*/
#define ENABLE            A6
#define MOTOR_0_1A        11
#define MOTOR_0_2A        5
#define MOTOR_1_1A        6  
#define MOTOR_1_2A        9
#define ENCODER_0_CHA     2
#define ENCODER_0_CHB     13
#define ENCODER_1_CHA     3
#define ENCODER_1_CHB     8

/*Infrared sensors definitions*/
#define IR0_TX       A1
#define IR1_TX       12
#define IR2_TX       7
#define IR3_TX       4
#define IR0_RX       A0
#define IR1_RX       A7
#define IR2_RX       A2
#define IR3_RX       A3

/*Extras*/
#define BUTTON      10

void motors_init(void);
void motor_0_speed(int speed, bool direction);
void motor_1_speed(int speed, bool direction);

void ir_init(void);
int ir_0_read(int delay);
int ir_1_read(int delay);
int ir_2_read(int delay);
int ir_3_read(int delay);

void gyro_init(void);
float gyro_get_yaw(float dt);

void control_forward(void);
void control_turn(float target_angle);

#endif

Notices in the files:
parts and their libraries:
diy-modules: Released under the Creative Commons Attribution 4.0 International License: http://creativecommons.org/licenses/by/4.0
